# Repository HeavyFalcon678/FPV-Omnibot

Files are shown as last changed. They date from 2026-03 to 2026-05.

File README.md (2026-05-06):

# FPV-Omnibot

Watch the video (https://www.youtube.com/watch?v=OyF7Ex0_O2U)

**Click the image above for a video demo ^^^. The .mp4 video is also in /media**

This a hack of the Crunch Labs Hack Pack Box #011 - Omnibot Forklift that unlocks its full potential and allows you do do fun things like:

- Add a 3D printed robotic gripper to pick things up
- Control the omnibot from a web dashboard on any device using the same network
- toggle a slow mode to enable precise maneuvering
- combine a camera with the web UI to add remote web streaming

To allow as many people as possible to upgrade their omnibots, I have added different configurations you can use:

- Slowmode (no extra hardware)
- Gripper (stock remote + gripper)
- Dashboard (stock omnibot + RPI)
- GripUI (gripper + RPI)
- FPV (RPI & camera, no gripper)
- LEGENDARY (gripper, RPI, & camera)

## Bill of Materials

1x Omnibot Forklift by Hack Pack

### Gripper

    1x MG90 or SG90 Servo
    4x M3x8 BHCS Screws
    2x M4x8 BHCS Screws
    2x M4x4x6 Heatset Inserts
    3x Male to Male Jumper wires
    3x Male to Female Jumper wires
    3D printed parts
    TPU filament or Grip Tape

### Web UI

    1x Raspberry Pi
    1x 5V battery pack & USB cable
    9x Female to Male Jumper wires

### Camera

    1x Raspberry Pi Camera 3 Wide
    1x 300mm
    4x M2x6 BHCS Screws
    4x M2 Nuts

## Instructions

### Gripper

Just put it together, it's pretty simple. Insert the heatsets, and the screw the screws in. Also make sure you screw the base to the mount _before_ you attach the arms, or you'll have to redo them.
For wiring, connect the servo to power and ground, and the signal wire to pin 10 on the Arduino.

### RPI

First set up the RPI as normal with the Raspberry Pi Imager. I'd recommend using Raspberry Pi OS Lite (64-bit), but you can use whatever you'd like. Make sure to write down your hostname, username, and password. MAKE SURE to **connect your pi to WiFi** and **enable SSH with password authentication**.

When you're finished, insert the SD card into the RPI and power it up. Wait a minute or so, and then connect it by `ssh username@password` and enter your password. It should log in, and then run this command:

`wget https://github.com/HeavyFalcon678/FPV-Omnibot/raw/main/forky.sh && . forky.sh install && . forky.sh run`

finally, run `echo "$(hostname -I | awk '{print $1}'):5000"` and write down what it prints. This is the url your web interface will be running on. Then reboot the PI and you're good to go.

On the hardware side, wire it up like this:

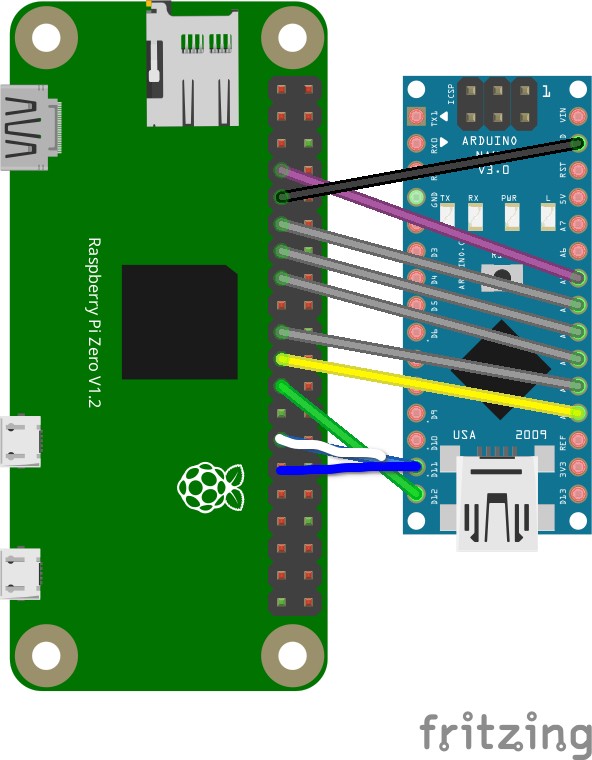
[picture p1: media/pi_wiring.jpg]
description


All RPI pin names are in BCM

```
RPI <-> ARDUINO
GPIO4  - A5
GPIO17 - A4
GPIO27 - A3
GPIO22 - A2
GPIO10 - A1
GPIO9  - A0
GPIO11 - D12
GPIO5  - D11
GND - GND
```

And finally, upload `arduino_code/pi.ino` and `arduino_code/config.h` to the arduino using [Crunchlabs IDE](https://ide.crunchlabs.com/editor/omnibot-forklift/3/StockCode/StockCode.ino).

### Camera

Follow the instructions to setup the Raspberry Pi, and then connect the ribbon cable to the designated CSI connectors.

To mount the camera, print the `picamera3_mount.step` file and fix the camera onto the mount with the M2 nuts and bolts. You can add the mount to the top screw of the servo. The software is the same, `arduino_code/pi.ino`.

## Usage

### No RPI

```
UP + L -> Open Gripper
UP + R -> Close Gripper
DN + L -> Toggle Slow Mode
```

### With RPI

The UI is pretty straightforward, just go to port 5000 on the ip address of your pi and all the buttons are self explanatory. On desktop there are some keyboard shortcuts though:

```
W -> Up
S -> Down
A -> Left
D -> Right
Q -> Rotate CCW
E -> Rotate CW
W+A -> Diagonal Left Up
W+D -> Diagonal Right Up
S+A -> Diagonal Left Down
S+D -> Diagonal Right Down
SPACE -> Toggle Fast/Slow
I -> Raise Fork
K -> Lower Fork
J -> Open Gripper
L -> Close Gripper
```

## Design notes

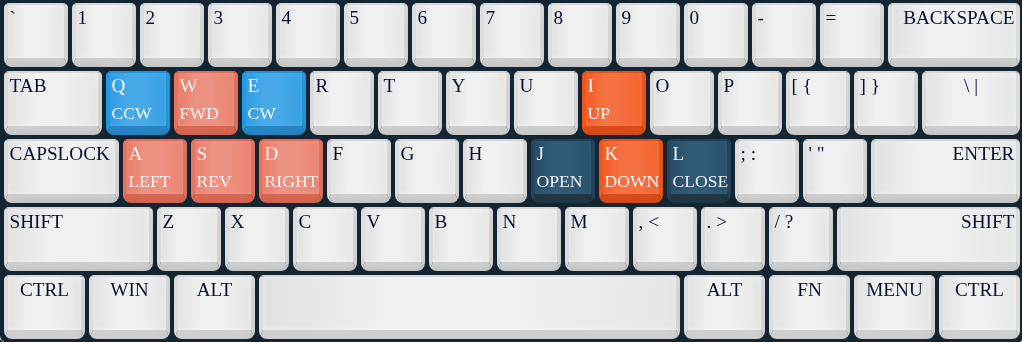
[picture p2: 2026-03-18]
static/assets/keymap.png

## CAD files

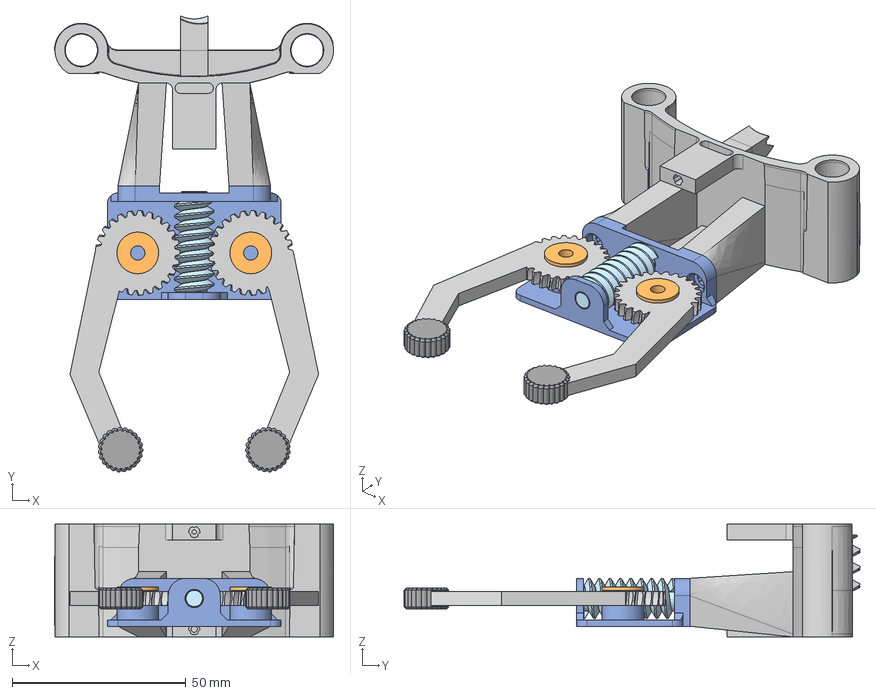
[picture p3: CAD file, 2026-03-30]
3d_files/gripper.step
80.3 x 131.3 x 32.5 mm

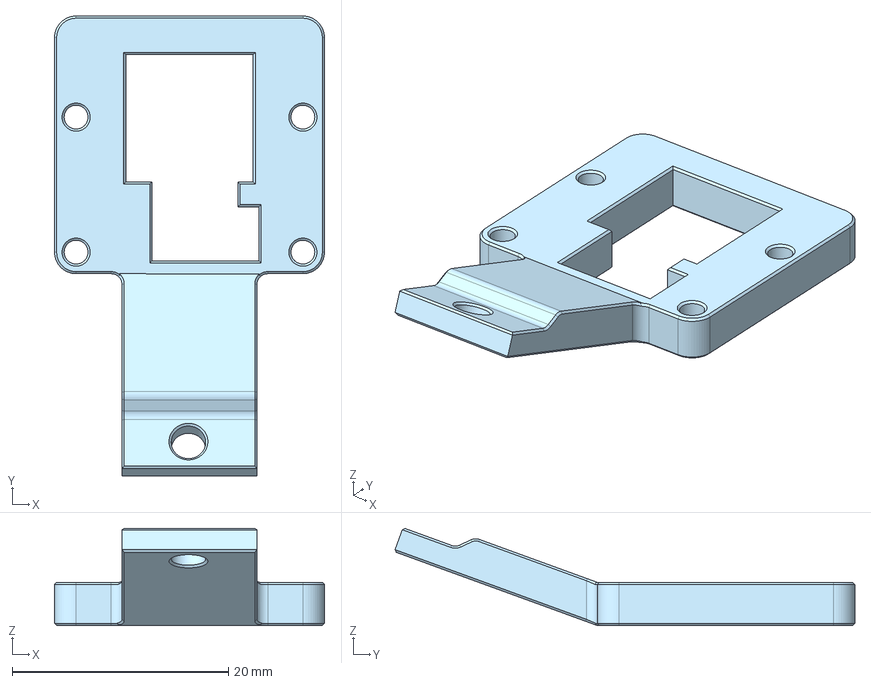
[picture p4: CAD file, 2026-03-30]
3d_files/picamera3_mount.step
25.0 x 42.6 x 8.99 mm

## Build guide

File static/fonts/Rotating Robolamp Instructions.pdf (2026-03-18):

## Description:

This hack combines the Robolamp remote hack with a "twist". Using only parts from other Hack Packs you can create The Rotating Robolamp. This hack creates base rotation for the robolamp. Base rotation allows your robot more freedom and flexibility to level up its assistance as your friendly light source. This hack also allows greater personality with moods seen best when in distracted mode; when distracted your robolamp will not just look away from what you need light on, it will rotate around to look at more interesting things than what you're working on. This hack includes Ir capabilities which allows the direction of light from a distance. Its sleek design allows for concealed battery packs while staying with the original Robolamp look. Including Ir abilities the lamp retains all button and joystick features seen in Robolamps stock code.

## Required Materials/Sensors:

- RoboLamp
- Wooden base and platform
piece from Card Dealer
- 15 short screw standoffs from Laser Tag
- 5 long screw standoffs from Label Maker
- Ir remote/sensor from Turret
- 1 gear motor from String Plotter
- Dual motor driver from String Plotter
- 3 male to male connectors from any robot
- 2 long metal M3 bolts from
Card Dealer

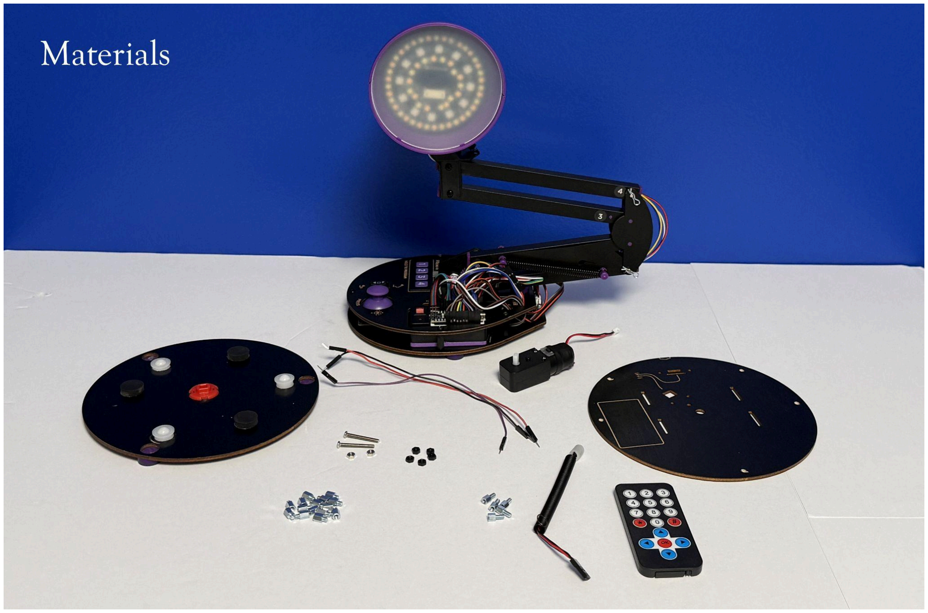
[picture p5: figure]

- 2 metal M3 nuts from Card Dealer
- Battery pack from any Hack Pack.

## Required Tools:

- Drill
- Sandpaper

## Assembly:

1. Grab the wooden base (Card Dealer), and pop out the transfer bearings.
2. In the wooden base, drill 7/16” holes ¼ inch away from the three transfer bearing hole (between the D-Shaft capture piece and original hole)
3. Widen the hole slightly by sanding the newly drilled holes until transfer bearings fit snuggly with sandpaper.
4. Place rubber feet from Robolamp in between the transfer bearings for stability.

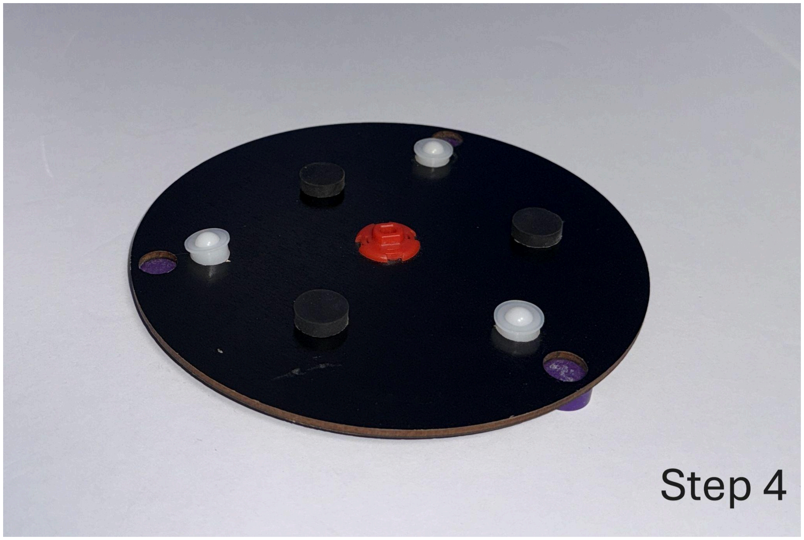
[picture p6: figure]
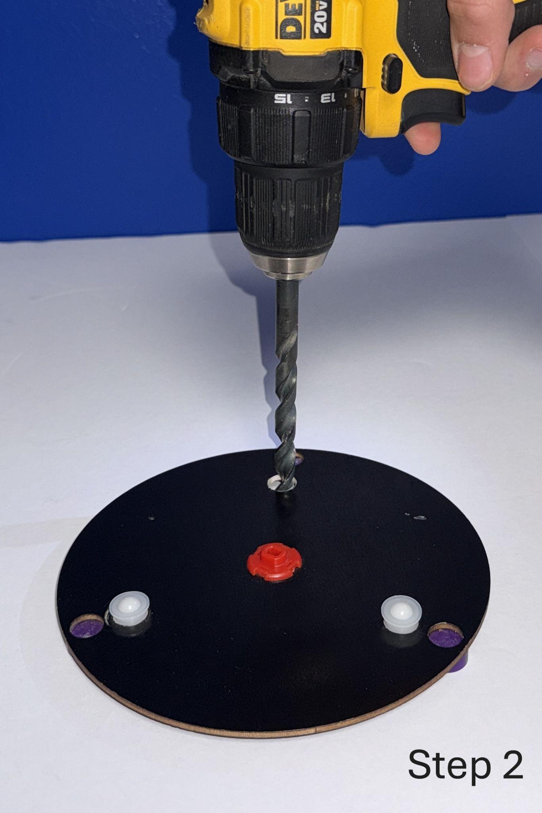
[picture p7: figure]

5. Get the wooden platform piece (Card Dealers) and gear motor (String plotter), align the gear motor to the wooden platform to thread 2 M3 nuts and bolts through holes provided.
6. Assemble together three short threaded standoffs (Laser Tag) and one long threaded standoff (Label Maker) making sure the long threaded standoff is visible on the bottom.

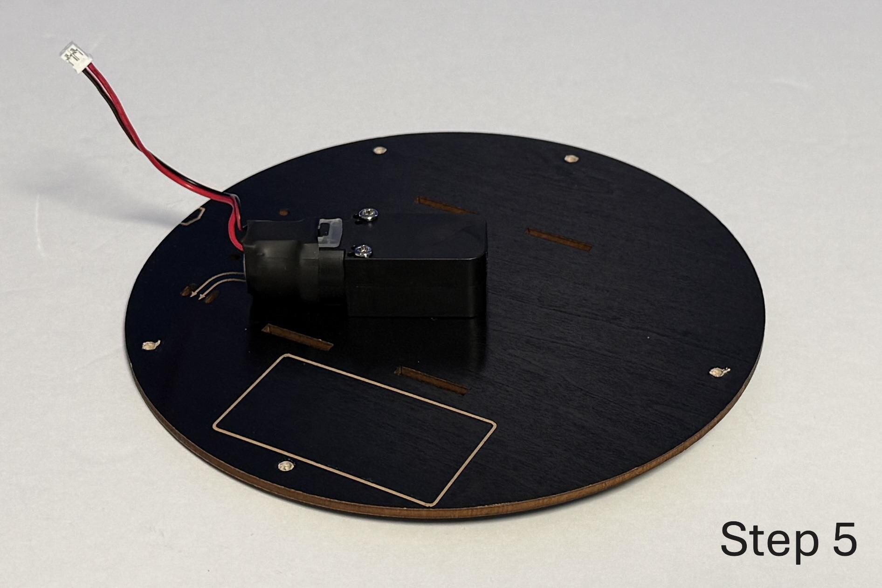
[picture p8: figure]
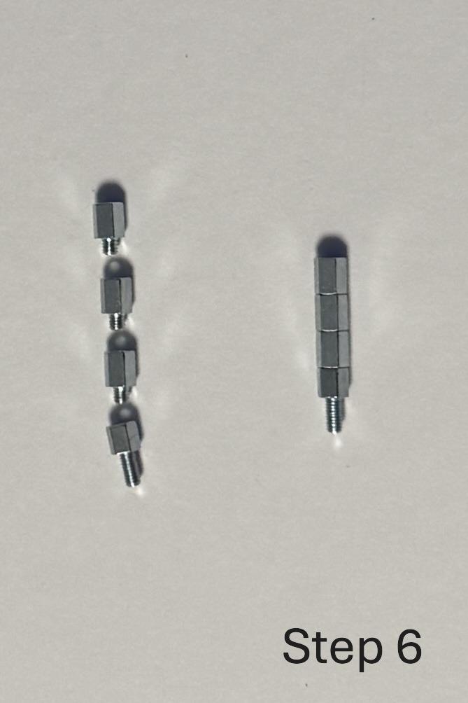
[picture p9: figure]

7. Repeat step 6, four more times for a total of five columns of standoffs.
8. Remove nuts from the base of the Robolamp.
9. Screw on the five standoff columns to the five open screws exposed in step 7.
10. Align the Robolamp with the platform piece so that the stepper motor’s wires are towards the back of the Robolamp.
11. Mark where the standoff columns touch the platform piece.
12. Drill ⅛” holes in the platform piece you marked in step 11.

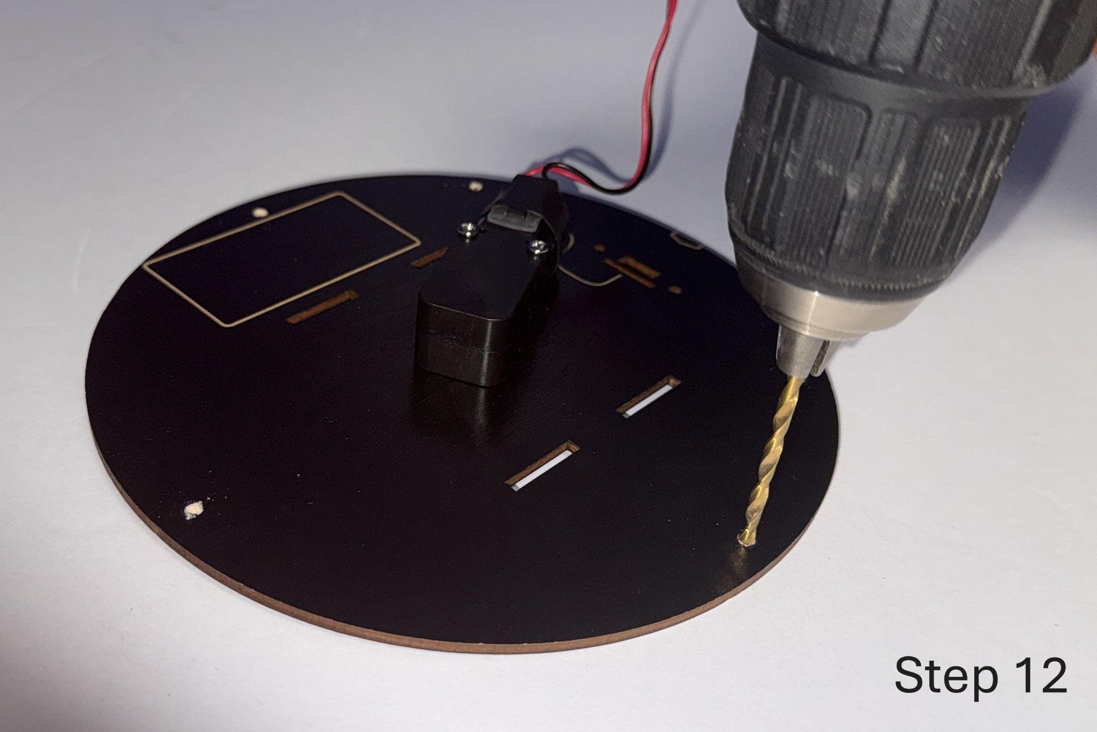
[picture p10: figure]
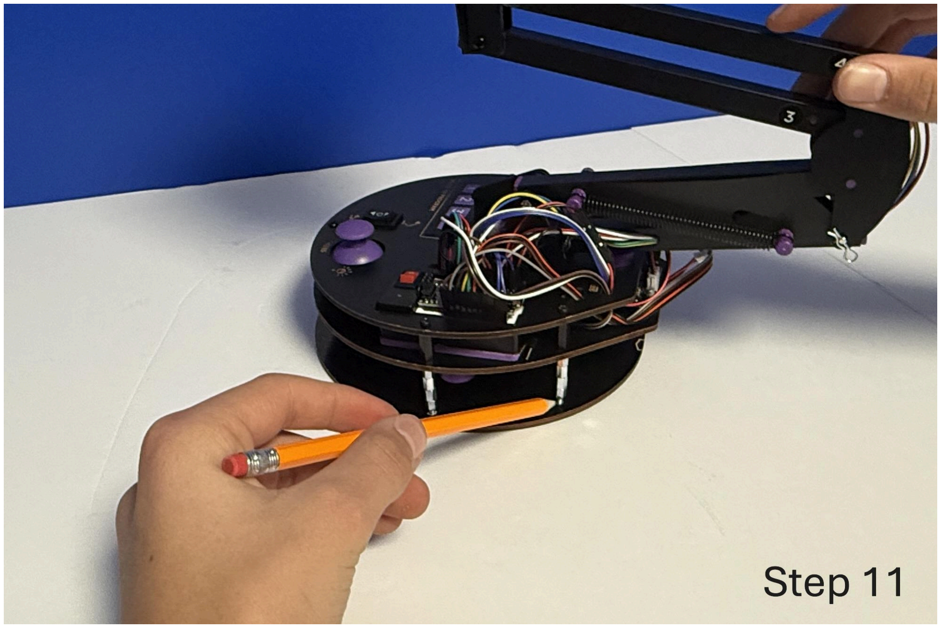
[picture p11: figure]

13. Connect platform piece to the Robolamp by sliding standoff columns through holes drilled and attach nuts to secure.
14. Replace the single motor driver with the dual motor driver (String Plotter).

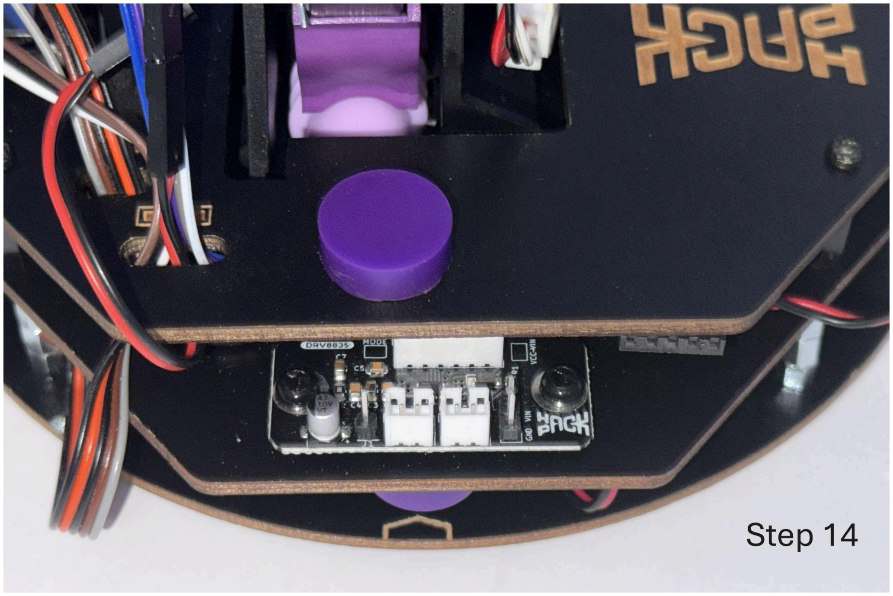
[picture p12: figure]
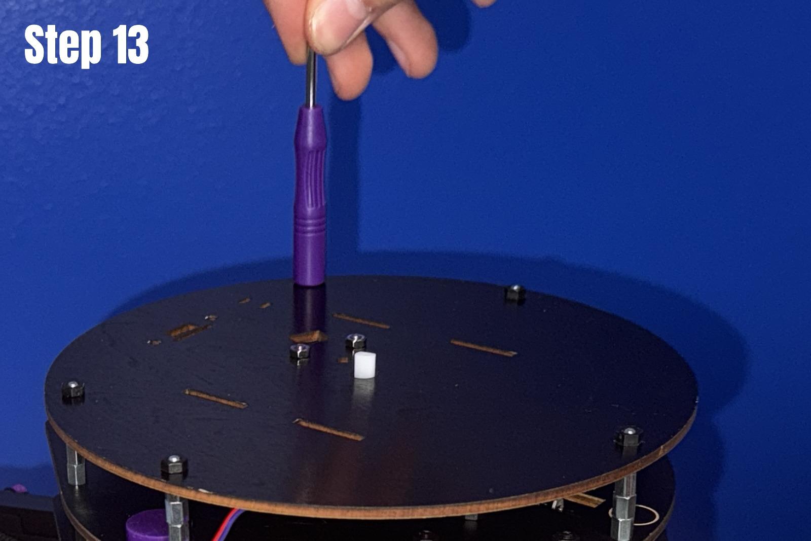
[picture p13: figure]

15. Attach the Ir receiver antenna connected to jumper wires (Ir Turret) to the Robolamp wearever you like the look of.
16. Place Robolamp onto a wooden base.
17. Slide the battery pack under the joystick next to the rotational motor.

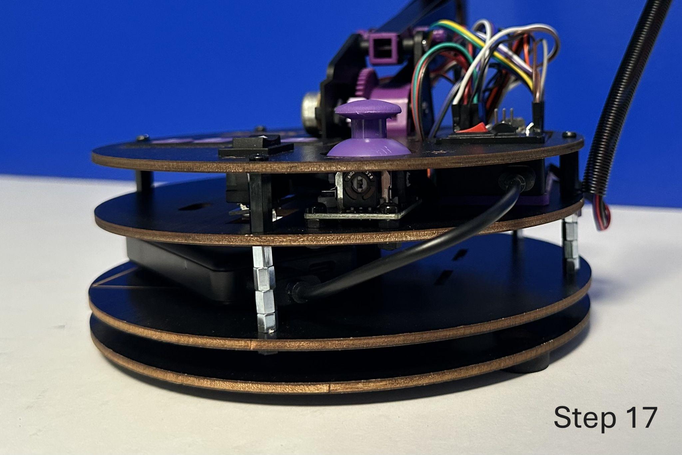
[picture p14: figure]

## Wiring:

A0 Height Potentiometer (White)
A1 Joy button (Orange)
A2 Base motor DIR to motor driver (White) A3 Lift motor PWM to motor driver (Grey) A4 Base motor DIR to motor driver (Purple) A5 Base motor PWM to motor driver (Blue) A6 Joy Yaw joystick (Purple)
A7 Joy Pitch (Green)
D2 IR Receiver (Jumper wire color)
D3 Btn3 (Grey)
D4 Btn4 (Brown)
D5 Warm LED (Yellow)
D6 Cool LED (Green)
D7 Btn2 (Orange)
D8 Btn1 (Black)
D9 ServoPitch (Purple)
D10 ServoYaw (White)
D11 Height MotorPWM (Blue)
D12 Height MotorDIR (Purple)
D13 NeoPixel LED (Blue)
GND -> Common Ground to all devices (Black) 5V -> To all devices (Red)

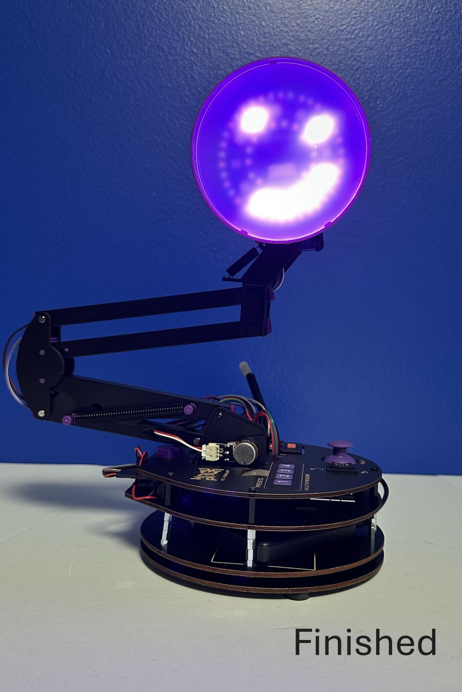
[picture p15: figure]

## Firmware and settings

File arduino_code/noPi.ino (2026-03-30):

/*
Huge thanks to those who have derived the kinematic conrrols for omni-directional robots. This hackpack comes with an optional educational reading that I highly reccomend: (Siradjuddin, Indrazno. "Kinematics and control a three wheeled omnidirectional mobile robot." Int. J. Electr. Electron. Eng 6.12 (2019): 1-6.) [https://www.internationaljournalssrg.org/IJEEE/2019/Volume6-Issue12/IJEEE-V6I12P101.pdf] 

Amazingly the relationship of the wheel speeds of the robot to its overall speed vector is algebraically linear.  The formula also works for any relative wheel angle and can easily be expanded to include more wheels. This gives a mathematically deterministic way to get the robot from A to B defined by two translation variables and one rotation variable, a powerful tool. 

Combining this with a gyroscope allows for a true field oriented drive-- where  joystick commands always will move the robot forwards relative to you, despite which way the robot is facing. For those of you willing to take on the challenge, this is a great hack to try!
*/

// Maximum motor duty cycle [0 - 255]
uint8_t maxSpeed = 255;
uint8_t slowSpeed = 100;
uint8_t currentSpeed = maxSpeed;

bool toggleSpeed = false;
int prevCommand = 0;

// motor flipping
bool flipM1 = false;
bool flipM2 = false;
bool flipM3 = false;
bool flipM4 = true;

#include "config.h"
#include <Servo.h>

#define RF_S1_V 19       // rf receiver signal pair 1, voltage
#define RF_S1_G 18       // rf receiver signal pair 1, ground
#define RF_S2_V 17
#define RF_S2_G 16
#define RF_S3_V 15
#define RF_S3_G 14
#define RF_S4_V 12
#define RF_S4_G 11

#define M1_DIR 4
#define M1_PWM 5
#define M2_DIR 7
#define M2_PWM 6
#define M3_DIR 8
#define M3_PWM 9

#define LIFT_DIR 2
#define LIFT_PWM 3

#define GRIPPER_PIN 10

//>>>>>>>>>>>>>>>>>>>>>>>>>> KEY ROBOT VARIABLES <<<<<<<<<<<<<<<<<<<<<<<<<<<<<<<
//RF Commands ----------------------------------------------------
// remote command: drive vector (in velocities) {v_x, v_y, omega}
int vSpeed[3];
// remote command: for forklift, -1 for lower, 0 for stay, 1 for move up
int moveFork = 0;
// for gripper, -1 for close, 0 for stay, 1 for open
int moveGripper = 0;
// stores the result of reciever message. 14 is default- dont move the motors.
int lastCommand[4] = {14, 14, 14, 14};
// robot will strafe when left/right is pressed and forward/back is held.
bool strafeMode = false;

//Robot Physical Parameters -------------------------------------
double angleWheel1 = 90.0;
double angleWheel2 = 210.0;
double angleWheel3 = 330.0;

// Equation puts wheel 1 facing forwards. This rotates the robot's "front" ccw.
double localAngle = 60.0;
//double gyroAngle;
// Radius of wheel center to robot center
double botRadius = 100.0;
// Radius of omniwheel
double wheelRadius = 35.0;

// stores each calculated wheel speed for a given commanded vector {w1, w2, w3}.
double wheelSpeeds[3];

// tuning paratmeter to get linearized motor speed.
double tune = 1; 

// strafing timer variable for catching odd remote behavior
unsigned long lastStrafe = 0;


bool flipGripper = false;
int gripperSpeed = 40; // 0-90 value, 90 is max. I'd recommend a low speed so you don't break your servo
int servoStopSpeed = 90;

Servo gripperServo;


// >>>>>>>>>>>>>>>>>>>>>>>>>>>>>>>>> SETUP <<<<<<<<<<<<<<<<<<<<<<<<<<<<<<<<<<<<<
void setup() {
  Serial.begin(115200);
  Serial.println("OMNIB V0.9.1 ..... (01/22/2025)");
  pinMode(RF_S1_V, INPUT_PULLUP);
  pinMode(RF_S1_G, INPUT_PULLUP);
  pinMode(RF_S2_V, INPUT_PULLUP);
  pinMode(RF_S2_G, INPUT_PULLUP);
  pinMode(RF_S3_V, INPUT_PULLUP);
  pinMode(RF_S3_G, INPUT_PULLUP);
  pinMode(RF_S4_V, INPUT_PULLUP);
  pinMode(RF_S4_G, INPUT_PULLUP);

  SoftPWMBegin();
  SoftPWMSet(3, 0);
  SoftPWMSet(9, 0);

  gripperServo.attach(GRIPPER_PIN);
  gripperServo.write(servoStopSpeed);

}



// >>>>>>>>>>>>>>>>>>>>>>>>>>>>>>>>> LOOP <<<<<<<<<<<<<<<<<<<<<<<<<<<<<<<<<<<<<<
void loop() {
  getDirection();
  moveBot();
  driveGripper();
}



// >>>>>>>>>>>>>>>>>>>>> RADIO COMMAND PROCESSING <<<<<<<<<<<<<<<<<<<<<<<<<<<<<<
// Read reciever input pins to decide what robot is going to do
void getDirection(){
  int command;

  // inputs stores meaured RF controller states, inputArr stores processed data 
  int inputArr[8];
  int inputs[8] = {1, 1, 1, 1, 1, 1, 1, 1};

  // create time variable
  unsigned long t = millis();

  // sample for 10ms for any pins going LOW. Deals with RF signal dropoouts.
  while(millis() < (t + 10)){
    if(digitalRead(RF_S1_G) == 0){
      inputs[0] = 0;
    }
    if(digitalRead(RF_S1_V) == 0){
      inputs[1] = 0;
    }
    if(digitalRead(RF_S2_G) == 0){
      inputs[2] = 0;
    }
    if(digitalRead(RF_S2_V) == 0){
      inputs[3] = 0;
    }
    if(digitalRead(RF_S3_G) == 0){
      inputs[4] = 0;
    }
    if(digitalRead(RF_S3_V) == 0){
      inputs[5] = 0;
    }
    if(digitalRead(RF_S4_G) == 0){
      inputs[6] = 0;
    }
    if(digitalRead(RF_S4_V) == 0){
      inputs[7] = 0;
    }
  }

  inputArr[0] = inputs[0];
  inputArr[1] = inputs[1];
  inputArr[2] = inputs[2];
  inputArr[3] = inputs[3];
  inputArr[4] = inputs[4];
  inputArr[5] = inputs[5];
  inputArr[6] = inputs[6];
  inputArr[7] = inputs[7];

  
  for(int i = 0; i < 8; i++){
    Serial.print(inputArr[i]);
    Serial.print(", ");
  }
  Serial.println();
  
  
  // These sequence of inputs are read when button/ button combos are pressed
  int F[8] = {1, 1, 0, 1, 1, 0, 1, 1};      // 1. forward
  int B[8] = {1, 1, 1, 0, 0, 1, 1, 1};      // 2. back
  int L[8] = {0, 1, 0, 1, 0, 1, 1, 1};      // 3. left
  int R[8] = {1, 0, 1, 0, 1, 0, 1, 1};      // 4. right
  int U[8] = {1, 1, 1, 1, 1, 1, 1, 0};      // 5. fork up
  int D[8] = {1, 1, 1, 1, 1, 1, 0, 1};      // 6. fork down
  int FL[8] = {0, 1, 0, 1, 1, 0, 1, 1};     // 7. forward + left
  int FR[8] = {1, 0, 0, 1, 1, 0, 1, 1};     // 8. forward + right
  int BL[8] = {0, 1, 1, 0, 0, 1, 1, 1};     // 9. back + left
  int BR[8] = {1, 0, 1, 0, 0, 1, 1, 1};     // 10. back + right
  int FU[8] = {1, 1, 0, 1, 1, 0, 1, 0};     // 11. forward + fork up
  int FD[8] = {1, 1, 0, 1, 1, 0, 0, 1};     // 12. forward + fork down
  int BU[8] = {1, 1, 1, 0, 0, 1, 1, 0};     // 13. back + fork up
  int BD[8] = {1, 1, 1, 0, 0, 1, 0, 1};     // 14. back + fork down
  int NONE[8] = {1, 1, 1, 1, 1, 1, 1, 1};   // 15. default, do nothing.
  int OPEN[8] = {0, 1, 0, 1, 0, 1, 1, 0};   // 16. open gripper
  int CLOSE[8] = {1, 0, 1, 0, 1, 0, 1, 0};  // 17. close gripper
  int SPEED[8] = {0, 1, 0, 1, 0, 1, 0, 1};  // 18. toggle speed



  //create array that enumerates every command 
  int cmdArr[18] = {0};

  // We loop through all pin readings and compare the number of matches for each command. One of the commands will match all 8 pin outputs and that is what will get chosen as the transmitter's result. cmdArr ranks the match value.
  // For example pressing the backwards button will generate a cmdArr =  {F = 0, B = 8, L = 4, R = 4, U = 4, D = 4, FL = 2, FR = 2, BL = 6, BR = 6, FU = 2, FD = 2, BU = 6, BD = 6, NONE = 4}. Thus backwards with a "match value" of 8 will be chosen.
  for(int i = 0; i < 8; i++){
    if(inputArr[i] == F[i]) cmdArr[0] += 1;
    if(inputArr[i] == B[i]) cmdArr[1] += 1;
    if(inputArr[i] == L[i]) cmdArr[2] += 1;
    if(inputArr[i] == R[i]) cmdArr[3] += 1;
    if(inputArr[i] == U[i]) cmdArr[4] += 1;
    if(inputArr[i] == D[i]) cmdArr[5] += 1;
    if(inputArr[i] == FL[i]) cmdArr[6] += 1;
    if(inputArr[i] == FR[i]) cmdArr[7] += 1;
    if(inputArr[i] == BL[i]) cmdArr[8] += 1;
    if(inputArr[i] == BR[i]) cmdArr[9] += 1;
    if(inputArr[i] == FU[i]) cmdArr[10] += 1;
    if(inputArr[i] == FD[i]) cmdArr[11] += 1;
    if(inputArr[i] == BU[i]) cmdArr[12] += 1;
    if(inputArr[i] == BD[i]) cmdArr[13] += 1;
    if(inputArr[i] == NONE[i]) cmdArr[14] += 1;
    if(inputArr[i] == OPEN[i]) cmdArr[15] += 1;
    if(inputArr[i] == CLOSE[i]) cmdArr[16] += 1;
    if(inputArr[i] == SPEED[i]) cmdArr[17] += 1;
  }

  for(int i = 0; i < 18; i++){
    if(cmdArr[i] == 8){
      command = i;
      break;
    }
  }
  
  toggleSpeed = false;
  
  // Assign speed vector values based on chosen command
  switch(command){
    case 0: //Forward
      vSpeed[0] = 0;
      vSpeed[1] = -1;
      vSpeed[2] = 0;
      moveFork = 0;
      moveGripper = 0;
      break;
    case 1: //Back
      vSpeed[0] = 0;
      vSpeed[1] = 1;
      vSpeed[2] = 0;
      moveFork = 0;
      moveGripper = 0;
      break;
    case 2: //Rotate Left (CCW)
      vSpeed[0] = 0;
      vSpeed[1] = 0;
      vSpeed[2] = -1;
      moveFork = 0;
      moveGripper = 0;
      break;
    case 3: //Rotate Right (CW)
      vSpeed[0] = 0;
      vSpeed[1] = 0;
      vSpeed[2] = 1;
      moveFork = 0;
      moveGripper = 0;
      break;
    case 4: //Fork Up
      vSpeed[0] = 0;
      vSpeed[1] = 0;
      vSpeed[2] = 0;
      moveFork = 1;
      moveGripper = 0;
      break;
    case 5: //Fork Down
      vSpeed[0] = 0;
      vSpeed[1] = 0;
      vSpeed[2] = 0;
      moveFork = -1;
      moveGripper = 0;
      break;
    case 6: //Forward + Left
      vSpeed[0] = 1;
      vSpeed[1] = -1;
      vSpeed[2] = 0;
      moveFork = 0;
      moveGripper = 0;
      break;
    case 7: //Forward + Right
      vSpeed[0] = -1;
      vSpeed[1] = -1;
      vSpeed[2] = 0;
      moveFork = 0;
      moveGripper = 0;
      break;
    case 8: //Back + Left
      vSpeed[0] = 1;
      vSpeed[1] = 1;
      vSpeed[2] = 0;
      moveFork = 0;
      moveGripper = 0;
      break;
    case 9: //Back + Right
      vSpeed[0] = -1;
      vSpeed[1] = 1;
      vSpeed[2] = 0;
      moveFork = 0;
      moveGripper = 0;
      break;
    case 10: //Forward + Fork Up
      vSpeed[0] = 0;
      vSpeed[1] = -1;
      vSpeed[2] = 0;
      moveFork = 1;
      moveGripper = 0;
      break;
    case 11:  //Forward + Fork Down
      vSpeed[0] = 0;
      vSpeed[1] = -1;
      vSpeed[2] = 0;
      moveFork = -1;
      moveGripper = 0;
      break;
    case 12: //Back + Fork Up
      vSpeed[0] = 0;
      vSpeed[1] = 1;
      vSpeed[2] = 0;
      moveFork = 1;
      moveGripper = 0;
      break;
    case 13: //Back + Fork Down
      vSpeed[0] = 0;
      vSpeed[1] = 1;
      vSpeed[2] = 0;
      moveFork = -1;
      moveGripper = 0;
      break;
    case 14: //None
      vSpeed[0] = 0;
      vSpeed[1] = 0;
      vSpeed[2] = 0;
      moveFork = 0;
      moveGripper = 0;
      break;
    case 15: //Open gripper
      vSpeed[0] = 0;
      vSpeed[1] = 0;
      vSpeed[2] = 0;
      moveFork = 0;
      moveGripper = 1;
      break;
    case 16: //Close gripper
      vSpeed[0] = 0;
      vSpeed[1] = 0;
      vSpeed[2] = 0;
      moveFork = 0;
      moveGripper = -1;
      break;
    case 17: // Toggle speed
      toggleSpeed = true;
      break;
    default:
      break;
  }


  if (prevCommand != command && toggleSpeed) {
    Serial.println("Yes");
    Serial.println("Yes");



    Serial.println("Yes");

    if (currentSpeed == maxSpeed) {
      currentSpeed = slowSpeed;
    } else {
      currentSpeed = maxSpeed;
    }
  }
  

  prevCommand = command;
  
  //Serial.println(command);

  // Add strafing / slide drive logic. Robot will strafe sideways (crabwalk) if left or right is pressed while the forward/back button is being held down. Users can the let go of forward/back after strafing has started and the slide drive behavior will persist.

  // first lets check that our command history contains initalizing strafe.
  bool initStrafe = false;

  for(int i = 0; i < 4; i++){
    // if command is 6, 7, 8, or 9
    if(lastCommand[i] > 5 && lastCommand[i] < 9){
      initStrafe = true;
      break;
    }
  }

  // If strafe is initalized, user can let go of forward/back
  if(initStrafe == true || strafeMode == true){
    if(command == 2){ // Left
      strafeMode = true;
      vSpeed[0] = -1;
      vSpeed[1] = 0;
      vSpeed[2] = 0;
      moveFork = 0;
      moveGripper = 0;
    } else if (command == 3){ // Right
      strafeMode = true;
      vSpeed[0] = 1;
      vSpeed[1] = 0;
      vSpeed[2] = 0;
      moveFork = 0;
      moveGripper = 0;
    } else {  // Other commands not related to strafe
      // check if this is a signal glitch, "debounces" radio commands
      if (lastCommand[0] == command && lastCommand[1] == command){
        strafeMode = false;
      } else {
        // do nothing
      }
    }
  }
  
  // if strafemode is active, the left and right button will slide the robot instead of rotating it.
  if(strafeMode){
    if(command == 2){ // Left
      vSpeed[0] = 1;
      vSpeed[1] = 0;
      vSpeed[2] = 0;
      moveFork = 0;
      moveGripper = 0;
    } else if (command == 3){ // Right
      vSpeed[0] = -1;
      vSpeed[1] = 0;
      vSpeed[2] = 0;
      moveFork = 0;
      moveGripper = 0;
    }
  }
  
  // Serial.print("X: ");
  // Serial.print(vSpeed[0]);
  // Serial.print(", Y: ");
  // Serial.print(vSpeed[1]);
  // Serial.print(", Omega: ");
  // Serial.print(vSpeed[2]);
  // Serial.print(". Fork Movement: ");
  // Serial.print(moveFork);
  // Serial.print(", Gripper Movement: ");
  // Serial.println(moveGripper);
  
  // shift the command history array down an element... 
  lastCommand[3] = lastCommand[2];
  lastCommand[2] = lastCommand[1];
  lastCommand[1] = lastCommand[0];
  // and save this excecuted command for next iteration
  lastCommand[0] = command;
}

// >>>>>>>>>>>>>>>>>>>>>>>> ROBOT ACTION FUNCTIONS <<<<<<<<<<<<<<<<<<<<<<<<<<<<<
// prepare motors to coorinate bot movements
void moveBot(){
  float wheelSpeeds[3];
  getWheelSpeeds(wheelSpeeds);
  driveWheels(wheelSpeeds, currentSpeed);
  driveLift();
  driveGripper();
}

// Addresses motor controllers to drive wheels at caclulated speeds
void driveWheels(float* speeds, float currentSpeed){  
  //drive all motors at calculated speeds
  float topWheelSpeed = max(max(abs(speeds[0]), abs(speeds[1])), abs(speeds[2]));

  wheelSpeeds[0] = speeds[0] / topWheelSpeed;
  wheelSpeeds[1] = speeds[1] / topWheelSpeed; 
  wheelSpeeds[2] = speeds[2] / topWheelSpeed;

  if(speeds[0] < 0){
    wheelSpeeds[0] = - pow(abs(wheelSpeeds[0]), tune) * currentSpeed;
  } else {
    wheelSpeeds[0] = pow(wheelSpeeds[0], tune) * currentSpeed;
  }
  if(speeds[1] < 0){
    wheelSpeeds[1] = - pow(abs(wheelSpeeds[1]), tune) * currentSpeed;
  } else {
    wheelSpeeds[1] = pow(wheelSpeeds[1], tune) * currentSpeed;
  }
  if(speeds[2] < 0){
    wheelSpeeds[2] = - pow(abs(wheelSpeeds[2]), tune) * currentSpeed;
  } else {
    wheelSpeeds[2] = pow(wheelSpeeds[2], tune) * currentSpeed;
  }

  if(flipM1){
     wheelSpeeds[0] = - wheelSpeeds[0];
  }
  if(flipM2){
     wheelSpeeds[1] = - wheelSpeeds[1];
  }
  if(flipM3){
     wheelSpeeds[2] = - wheelSpeeds[2];
  }
  

  if(wheelSpeeds[0] < 0){
    digitalWrite(M1_DIR, LOW);
  } else {
    digitalWrite(M1_DIR, HIGH);
  }
  analogWrite(M1_PWM, int(abs(wheelSpeeds[0])));

  if(wheelSpeeds[1] < 0){
    digitalWrite(M2_DIR, LOW);
  } else {
    digitalWrite(M2_DIR, HIGH);
  }
  analogWrite(M2_PWM, int(abs(wheelSpeeds[1])));

  if(wheelSpeeds[2] < 0){
    digitalWrite(M3_DIR, LOW);
  } else {
    digitalWrite(M3_DIR, HIGH);
  }
  SoftPWMSet(M3_PWM, int(abs(wheelSpeeds[2])));
}

// Moves lift motor. full forward, full back, or stopped.
void driveLift(){
  if(flipM4){
    if(moveFork > 0){
      digitalWrite(LIFT_DIR, LOW);
      SoftPWMSet(LIFT_PWM, 255);
    } else if(moveFork < 0){
      digitalWrite(LIFT_DIR, HIGH);
      SoftPWMSet(LIFT_PWM, 255);
    } else{
      digitalWrite(LIFT_DIR, HIGH);
      SoftPWMSet(LIFT_PWM, 0);
    }
  } else {
    if(moveFork > 0){
      digitalWrite(LIFT_DIR, HIGH);
      SoftPWMSet(LIFT_PWM, 255);
    } else if(moveFork < 0){
      digitalWrite(LIFT_DIR, LOW);
      SoftPWMSet(LIFT_PWM, 255);
    } else{
      digitalWrite(LIFT_DIR, LOW);
      SoftPWMSet(LIFT_PWM, 0);
    }
  }
}


void driveGripper() {
  // Serial.println("Driving Gripper");
  if(flipGripper){
    if(moveGripper > 0){
      gripperServo.write(servoStopSpeed + gripperSpeed);
    } else if(moveGripper < 0){
      gripperServo.write(servoStopSpeed - gripperSpeed);
    } else{
      // Serial.println("Servo stop");
      gripperServo.write(servoStopSpeed);
    }
  } else {
    if(moveGripper > 0){
      // Serial.println("Servo go");
      gripperServo.write(servoStopSpeed - gripperSpeed);
    } else if(moveGripper < 0){
      gripperServo.write(servoStopSpeed + gripperSpeed);
    } else{
      // Serial.println("Servo stop");
      gripperServo.write(servoStopSpeed);
    }
  }
}





// >>>>>>>>>>>>>>>>>>>>>>>>>> INVERSE KINEMATICS <<<<<<<<<<<<<<<<<<<<<<<<<<<<<<<
// calculates speed of each wheel based of commanded speed vector. Forumlas are in the linked reading!
void getWheelSpeeds(float* wheelList) {
  double botAngle = localAngle; //+ gyroAngle;

  // 0.0174533 converts deg to rad 
  wheelList[0] = (-sin((botAngle + angleWheel1) * 0.0174533) 
                * cos(botAngle * 0.0174533) * vSpeed[0] + cos((botAngle + angleWheel1) * 0.0174533) * cos(botAngle * 0.0174533) * vSpeed[1] + botRadius * vSpeed[2]) / wheelRadius;
  
  wheelList[1] = (-sin((botAngle + angleWheel2) * 0.0174533) 
                * cos(botAngle * 0.0174533) * vSpeed[0] + cos((botAngle + angleWheel2) * 0.0174533) * cos(botAngle * 0.0174533) * vSpeed[1] + botRadius * vSpeed[2])/ wheelRadius;
  wheelList[2] = (-sin((botAngle + angleWheel3) * 0.0174533) 
                * cos(botAngle * 0.0174533) * vSpeed[0] + cos((botAngle + angleWheel3) * 0.0174533) * cos(botAngle * 0.0174533) * vSpeed[1] + botRadius * vSpeed[2])/ wheelRadius;         
}

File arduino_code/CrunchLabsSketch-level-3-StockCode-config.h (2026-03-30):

#ifndef SOFTPWM_COMBINED_H
#define SOFTPWM_COMBINED_H

#include <Arduino.h>
#include <avr/io.h>
#include <avr/interrupt.h>

/* ================= TIMER DEFINITIONS (SoftPWM_timer.h) ================= */

#if defined(__AVR_ATmega32U4__)
#define USE_TIMER4_HS
#elif defined(__arm__) && defined(TEENSYDUINO)
#define USE_INTERVALTIMER
#else
#define USE_TIMER2
#endif

#if defined(USE_TIMER2)

#define SOFTPWM_TIMER_INTERRUPT TIMER2_COMPA_vect
#define SOFTPWM_TIMER_SET(val) (TCNT2 = (val))
#define SOFTPWM_TIMER_INIT(ocr) ({ \
  TIFR2 = (1 << TOV2); \
  TCCR2B = (1 << CS21); \
  TCCR2A = (1 << WGM21); \
  OCR2A = (ocr); \
  TIMSK2 = (1 << OCIE2A); \
})

#elif defined(USE_TIMER4_HS)

#define SOFTPWM_TIMER_INTERRUPT TIMER4_COMPA_vect
#define SOFTPWM_TIMER_SET(val) (TCNT4 = (val))
#define SOFTPWM_TIMER_INIT(ocr) ({ \
  TCCR4A = 0; \
  TCCR4B = 0x04; \
  TCCR4C = 0; \
  TCCR4D = 0; \
  TCCR4E = 0; \
  OCR4C = (ocr); \
  TIMSK4 = (1 << OCIE4A); \
})

#elif defined(USE_INTERVALTIMER)

#define SOFTPWM_TIMER_INTERRUPT softpwm_interval_timer
#ifdef ISR
#undef ISR
#endif
#define ISR(f) void f(void)
#define SOFTPWM_TIMER_SET(val)
#define SOFTPWM_TIMER_INIT(ocr) ({ \
  IntervalTimer *t = new IntervalTimer(); \
  t->begin(softpwm_interval_timer, 1000000.0 / (float)(SOFTPWM_FREQ * 256)); \
})

#endif

/* ================= ORIGINAL DEFINITIONS ================= */

#ifndef SOFTPWM_MAXCHANNELS
#define SOFTPWM_MAXCHANNELS 20
#endif

#define SOFTPWM_NORMAL 0
#define SOFTPWM_INVERTED 1

#if F_CPU
#define SOFTPWM_FREQ 60UL
#define SOFTPWM_OCR (F_CPU/(8UL*256UL*SOFTPWM_FREQ))
#else
#define SOFTPWM_OCR 130
#endif

volatile uint8_t _isr_softcount = 0xff;
uint8_t _softpwm_defaultPolarity = SOFTPWM_NORMAL;

typedef struct
{
  int8_t pin;
  uint8_t polarity;
  volatile uint8_t *outport;
  uint8_t pinmask;
  uint8_t pwmvalue;
  uint8_t checkval;
  uint8_t fadeuprate;
  uint8_t fadedownrate;
} softPWMChannel;

softPWMChannel _softpwm_channels[SOFTPWM_MAXCHANNELS];

/* ================= ISR ================= */

ISR(SOFTPWM_TIMER_INTERRUPT)
{
  uint8_t i;
  int16_t newvalue;
  int16_t direction;

  if(++_isr_softcount == 0)
  {
    for (i = 0; i < SOFTPWM_MAXCHANNELS; i++)
    {
      if (_softpwm_channels[i].fadeuprate > 0 || _softpwm_channels[i].fadedownrate > 0)
      {
        direction = _softpwm_channels[i].pwmvalue - _softpwm_channels[i].checkval;
        newvalue = _softpwm_channels[i].pwmvalue;

        if (direction > 0 && _softpwm_channels[i].fadeuprate > 0)
        {
          newvalue = _softpwm_channels[i].checkval + _softpwm_channels[i].fadeuprate;
          if (newvalue > _softpwm_channels[i].pwmvalue)
            newvalue = _softpwm_channels[i].pwmvalue;
        }
        else if (direction < 0 && _softpwm_channels[i].fadedownrate > 0)
        {
          newvalue = _softpwm_channels[i].checkval - _softpwm_channels[i].fadedownrate;
          if (newvalue < _softpwm_channels[i].pwmvalue)
            newvalue = _softpwm_channels[i].pwmvalue;
        }

        _softpwm_channels[i].checkval = newvalue;
      }
      else
        _softpwm_channels[i].checkval = _softpwm_channels[i].pwmvalue;

      if (_softpwm_channels[i].checkval > 0)
      {
        if (_softpwm_channels[i].polarity == SOFTPWM_NORMAL)
          *_softpwm_channels[i].outport |= _softpwm_channels[i].pinmask;
        else
          *_softpwm_channels[i].outport &= ~(_softpwm_channels[i].pinmask);
      }
    }
  }

  for (i = 0; i < SOFTPWM_MAXCHANNELS; i++)
  {
    if (_softpwm_channels[i].pin >= 0)
    {
      if (_softpwm_channels[i].checkval == _isr_softcount)
      {
        if (_softpwm_channels[i].polarity == SOFTPWM_NORMAL)
          *_softpwm_channels[i].outport &= ~(_softpwm_channels[i].pinmask);
        else
          *_softpwm_channels[i].outport |= (_softpwm_channels[i].pinmask);
      }
    }
  }
}

/* ================= FUNCTIONS ================= */

void SoftPWMBegin(uint8_t defaultPolarity = SOFTPWM_NORMAL)
{
  uint8_t i;

  SOFTPWM_TIMER_INIT(SOFTPWM_OCR);

  for (i = 0; i < SOFTPWM_MAXCHANNELS; i++)
  {
    _softpwm_channels[i].pin = -1;
    _softpwm_channels[i].polarity = SOFTPWM_NORMAL;
    _softpwm_channels[i].outport = 0;
    _softpwm_channels[i].fadeuprate = 0;
    _softpwm_channels[i].fadedownrate = 0;
  }

  _softpwm_defaultPolarity = defaultPolarity;
}
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

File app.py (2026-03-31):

from flask import Flask, render_template, request, Response
from gpiozero import Device, OutputDevice
from picamera2 import Picamera2
import cv2



rf1 = OutputDevice(4)
rf2 = OutputDevice(17)
rf3 = OutputDevice(27)
rf4 = OutputDevice(22)
rf5 = OutputDevice(10)
rf6 = OutputDevice(9)
rf7 = OutputDevice(11)
rf8 = OutputDevice(5)

rf1.value = 1
rf2.value = 1
rf3.value = 1
rf4.value = 1
rf5.value = 1
rf6.value = 1
rf7.value = 1
rf8.value = 1


app = Flask(__name__)

cameraConnected = False

try:
    picam2 = Picamera2()

    config = picam2.create_video_configuration(
        main={"size": (640, 480), "format": "RGB888"}
    )

    picam2.configure(config)

    picam2.start()
    cameraConnected = True
except Exception:
    pass


def generateFrames():
    while True:
        frame = picam2.capture_array()
        frame = cv2.flip(frame, -1)
        ret, buffer = cv2.imencode('.jpg', frame, [cv2.IMWRITE_JPEG_QUALITY, 80])
        frame = buffer.tobytes()
        yield (
            b'--frame\r\n'
            b'Content-Type: image/jpeg\r\n\r\n' +
            frame +
            b'\r\n'
        )


@app.route('/')
def index():
    return render_template('index.html')


@app.route('/video')
def video():
    return Response(generateFrames(), mimetype='multipart/x-mixed-replace; boundary=frame')


@app.route('/camera-status')
def status():
    if (cameraConnected):
        return "connected"
    else:
        return "not connected"



@app.route('/control', methods=['POST'])
def handle_info():
    json = request.get_json()
    print("Type:", json["type"], "Info:", json["info"])

    if (json["type"] == "Move"):
        if (json["info"] == "Forward"):
            sendToArduino("1, 1, 0, 1, 1, 0, 1, 1")
        elif json["info"] == "Backward":
            sendToArduino("1, 1, 1, 0, 0, 1, 1, 1")
        elif json["info"] == "Left":
            sendToArduino("0, 0, 0, 0, 1, 1, 1, 1")
        elif json["info"] == "Right":
            sendToArduino("1, 1, 1, 1, 0, 0, 0, 0")
        elif json["info"] == "Forward Left":
            sendToArduino("0, 1, 0, 1, 1, 0, 1, 1")
        elif json["info"] == "Forward Right":
            sendToArduino("1, 0, 0, 1, 1, 0, 1, 1")
        elif json["info"] == "Backward Left":
            sendToArduino("0, 1, 1, 0, 0, 1, 1, 1")
        elif json["info"] == "Backward Right":
            sendToArduino("1, 0, 1, 0, 0, 1, 1, 1")
        elif json["info"] == "CW":
            sendToArduino("0, 1, 0, 1, 0, 1, 1, 1")
        elif json["info"] == "CCW":
            sendToArduino("1, 0, 1, 0, 1, 0, 1, 1")
        elif json["info"] == "None":
            sendToArduino("1, 1, 1, 1, 1, 1, 1, 1")

    elif json["type"] == "Fast":
        if json["info"] == True:
            sendToArduino("0, 1, 0, 1, 0, 1, 0, 1")
        elif json["info"] == False:
            sendToArduino("0, 1, 1, 0, 0, 0, 1, 1")

    elif json["type"] == "Fork":
        if json["info"] == "Up":
            sendToArduino("1, 1, 1, 1, 1, 1, 1, 0")
        elif json["info"] == "Down":
            sendToArduino("1, 1, 1, 1, 1, 1, 0, 1")
        elif json["info"] == "None":
            sendToArduino("1, 1, 1, 1, 1, 1, 1, 1")
        

    elif json["type"] == "Gripper":
        if json["info"] == "Open":
            sendToArduino("0, 1, 0, 1, 0, 1, 1, 0")
        elif json["info"] == "Close":
            sendToArduino("1, 0, 1, 0, 1, 0, 1, 0")
        elif json["info"] == "None":
            sendToArduino("1, 1, 1, 1, 1, 1, 1, 1")
    





    return "OK"


def sendToArduino(signal):
    signals = signal.split(", ")

    print(signals)
    rf1.value = int(signals[0])
    rf2.value = int(signals[1])
    rf3.value = int(signals[2])
    rf4.value = int(signals[3])
    rf5.value = int(signals[4])
    rf6.value = int(signals[5])
    rf7.value = int(signals[6])
    rf8.value = int(signals[7])



if __name__ == '__main__':
    app.run(host='0.0.0.0', port=5000, debug=False, use_reloader=False)

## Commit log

2026-03-18 Change button management and fix UI
    [app.py]
2026-03-19 First prototype
2026-03-20 Flip rotation buttons
2026-03-20 Add initial support for camera
2026-03-20 Fix color encoding and flip output
    [app.py]
2026-03-20 fix camera output
2026-03-20 fix camera output again
    [app.py]
2026-03-23 Fix camera stream
2026-03-23 Start styling camera
2026-03-24 add mobile camera
2026-03-30 update README.md and install script, add 3d files and arduino code
    [gripper.step, picamera3_mount.step]
2026-03-30 add camera checking
2026-03-30 update camera things
2026-03-30 update camera code
2026-03-31 update camera styling
